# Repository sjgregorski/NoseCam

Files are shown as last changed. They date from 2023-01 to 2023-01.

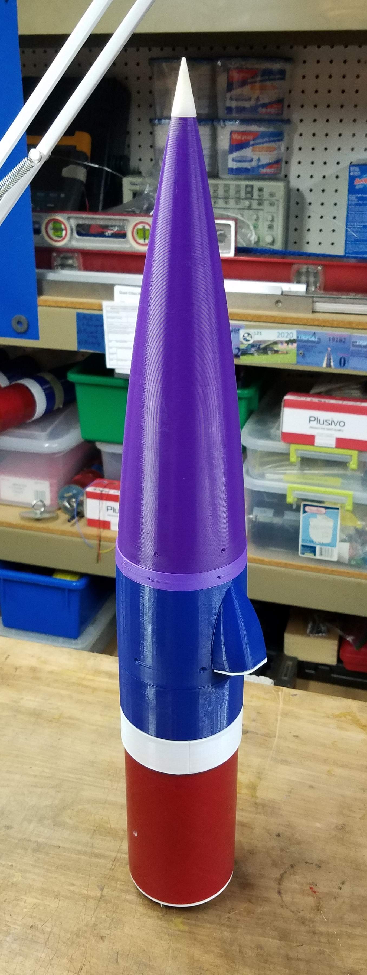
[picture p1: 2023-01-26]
Step 5 - Final Assembly/Build Photos/2023-01-22_019.jpg

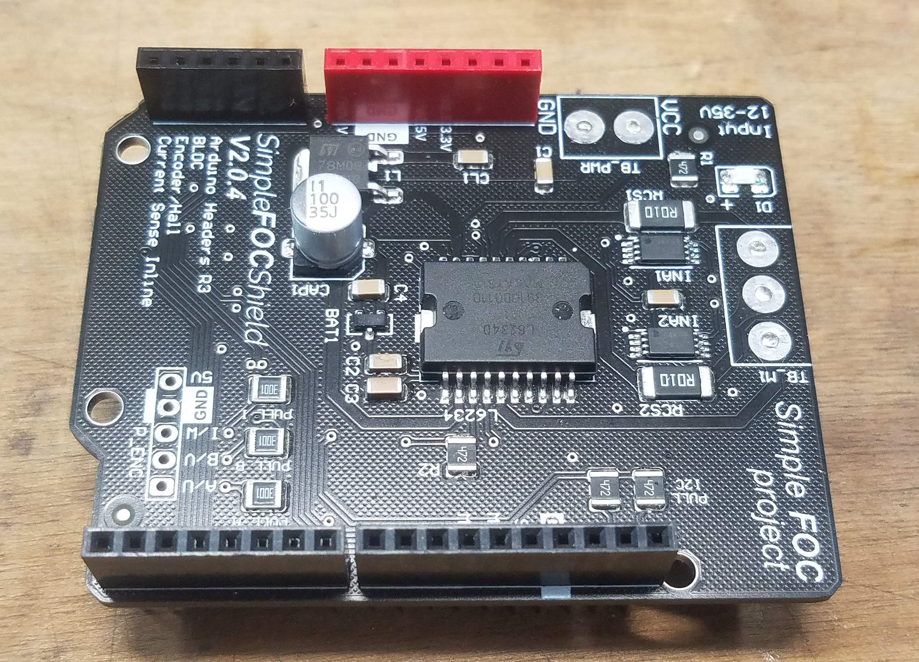
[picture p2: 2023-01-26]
Step 3 - Build the Circuit Board Stack/Build Photos/2023-01-11_013.jpg

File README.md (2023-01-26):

# NoseCam  

NoseCam is something I created to stabilize (de-spin) high power rocket flight videos.  It also forms the basis for a Vertical Orientation Control (VOC) system.  What I am sharing in this distribution does NOT contain info on the VOC subsystem.  That being said, if you manage to successfully build and fly a NoseCam using what I am sharing here then you are 90% of the way to having a VOC system.  Almost everything you need is already here.  You “just” have to add the needed components to the upper nose (servo(s), winglets/canards, etc.) and write some additional code.  

The Rocketry Form (TRF) is where I have been posting everything I’ve been doing with NoseCam.  Here are some useful links to posts:

https://www.rocketryforum.com/threads/a-new-spin-on-vertical-orientation-control.174525/

https://www.rocketryforum.com/threads/falcon-nosecam-build-thread.174591/

https://www.rocketryforum.com/threads/two-stage-flight-with-video-stabilization.172553/

I plan on continuing to use TRF as the only location where I will answer questions.  So if you have a question, post it to the “Falcon NoseCam Build Thread” on TRF.

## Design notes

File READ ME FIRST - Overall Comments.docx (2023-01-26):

NoseCam is something I created to stabilize (de-spin) high power rocket flight videos. It also forms the basis for a Vertical Orientation Control (VOC) system. What I am sharing in this distribution does NOT contain info on the VOC subsystem. That being said, if you manage to successfully build and fly a NoseCam using what I am sharing here then you are 90% of the way to having a VOC system. Almost everything you need is already here. You “just” have to add the needed components to the upper nose (servo(s), winglets/canards, etc.) and write some additional code.

The Rocketry Form (TRF) is where I have been posting everything I’ve been doing with NoseCam. Here are some useful links to posts:

https://www.rocketryforum.com/threads/a-new-spin-on-vertical-orientation-control.174525/

https://www.rocketryforum.com/threads/falcon-nosecam-build-thread.174591/

https://www.rocketryforum.com/threads/two-stage-flight-with-video-stabilization.172553/

I plan on continuing to use TRF as the only location where I will answer questions. So if you have a question, post it to the “Falcon NoseCam Build Thread” on TRF.

What I have provided in this distribution is intended to be a STARTING POINT. It is NOT a complete, soup-to-nuts set of instructions that would allow anyone to build a NoseCam. That would have been far too much work to create. (Sorry) Simply put, if you are going to build one of these things, you are going to need to maintain and tune it. And before you can do those things, you need to understand it. So being an active participant in the overall process (and not just a user) is critical. I’m sure there are things missing in this distribution (such as overall schematics LOL). I’m also very sure there are things wrong that I haven’t found yet. This has been and always will be a research project for me. It is also a work in progress. I consider the Arduino code to be the closest thing there will be to an instruction manual. (Again, sorry) And unfortunately, I write mediocre code at best !

In truth, I don’t have any expectations that someone will build an exact copy of what I have shared here. What I do hope is that like-minded folks can take what I have shared and use some part of it (code, design concepts, etc.) to build something cool for themselves. That being said, if you do try to build a NoseCam using what I have provided here, then you will already need to be VERY GOOD with the following skills:

- High Power Rocketry (HPR) – I have been building and flying for many years and have performed hundreds of high power / electronic dual deploy / GPS tracker flights. I’ve also done a lot of high power two-stage flights. The NoseCam by itself can be a handful to use when you first start out, so it helps if the “rocketry” part of using it is very familiar to you.
- 3D CAD (I use Fusion 360)
  - Modifying / tweaking CAD part files to meet your particular needs
- 3D Printing (and modifying printed parts to fit)
  - These are structural parts going into a rocket. They need strength. PLA printers need not apply.
- Arduino coding and debugging (LOTS and LOTS of debugging)
  - Be prepared to spend a LOT of time mastering the SimpleFOC Arduino library
- Overall mechanical design and fabrication skills
- Electronic design, assembly and debugging (LOTS and LOTS of debugging)

Things you will need:

- Money – I’ve spent several thousand dollars on this. You will spend less, but you will still spend a lot. Plan on buying two or three of everything needed. You will fry / break / trash / crash a lot of stuff. If you buy one set of everything and get it to work and it lasts more than one flight you are a genius.
- Time – I’ve easily spent over 1000 hours developing this. I’ve built several NoseCams, and even with all my experience it takes about 50 hours to build a new one. For someone starting from scratch you should plan on many months of fabrication, learning and mistakes.
- Access to a machine shop / maker space is really helpful. You will definitely need a 3D printer and an electronics assembly bench. Standard debugging tools (DVM, O-Scope, solder rework tools) are a must.

Other stuff:

- There are a lot of “READ ME” files in the various folders. You really want to read all of them. It will save you a LOT of time.
- My expectation is that reading the NoseCam Arduino code will provide enough of an “instruction manual” to get you going. My commenting isn’t great, but it is there. I know it’s a lot of code. But understanding it will be good for you. Just like eating kale ….
- I use Bluetooth classic and my Android phone to communicate with the NoseCam. You can’t use the NoseCam without some way of communicating over Bluetooth. There’s a wonderful Android phone app called “Bluetooth Terminal HC-05 Pro” that I use.

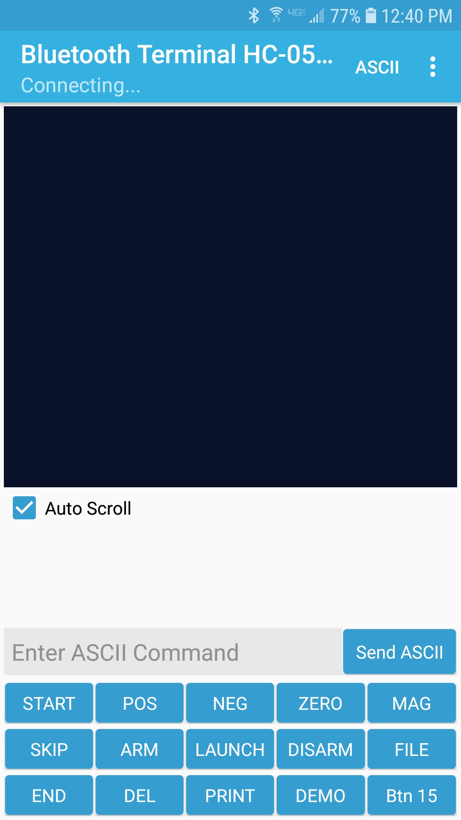
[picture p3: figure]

- The NoseCam Arduino code has data logging for every flight. The data is stored to the 2MB flash on the Adafruit Metro M4. Unfortunately ………….
  - Getting the data off of the NoseCam and into a useful format like Excel is ugly.
    - I connect to the NoseCam with my laptop via Bluetooth
    - I open the Arduino IDE and use the serial monitor to enter the needed commands to get the NoseCam to start streaming the logged data from a particular file to the laptop serial monitor
    - Once the file is done streaming to the serial monitor, I copy-and-paste the data from the serial monitor to a .txt file on my laptop
    - I then open the .txt file as a .csv file in Excel
    - I told you it was ugly
  - I download data after every flight and then delete the data file from the NoseCam since there is only 2MB of flash storage there. I have no idea how many data files can be written to the flash before some weird file management error occurs. You have been warned 😊
- I’ll put this info here and repeat it in other places
  - Use the 1.7.5 version of the Adafruit SAMD board library for the Metro M4. Do NOT use the latest version. It will not work. I have no idea why.
  - Use the SimpleFOC libraries I have provided it this distribution. They are an older version but they work. Do NOT try to download and use the latest version of the libraries. They will not work. I have no idea why.
    - Just FYI, my SimpleFOC libraries have two slight modifications which make synchronizing the BLDC motor to the encoder less aggressive.

That’s it ! Good luck !!!!!!!

Steve Gregorski

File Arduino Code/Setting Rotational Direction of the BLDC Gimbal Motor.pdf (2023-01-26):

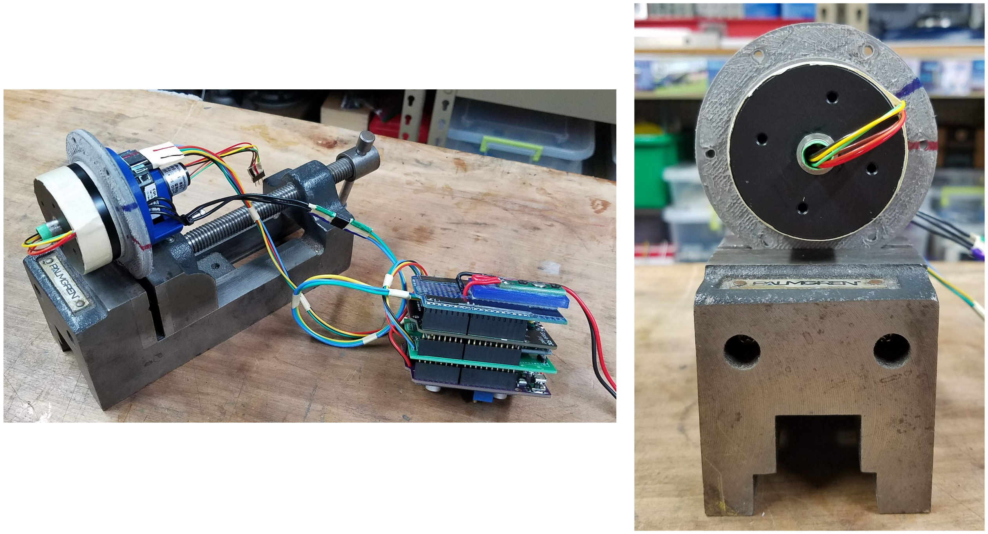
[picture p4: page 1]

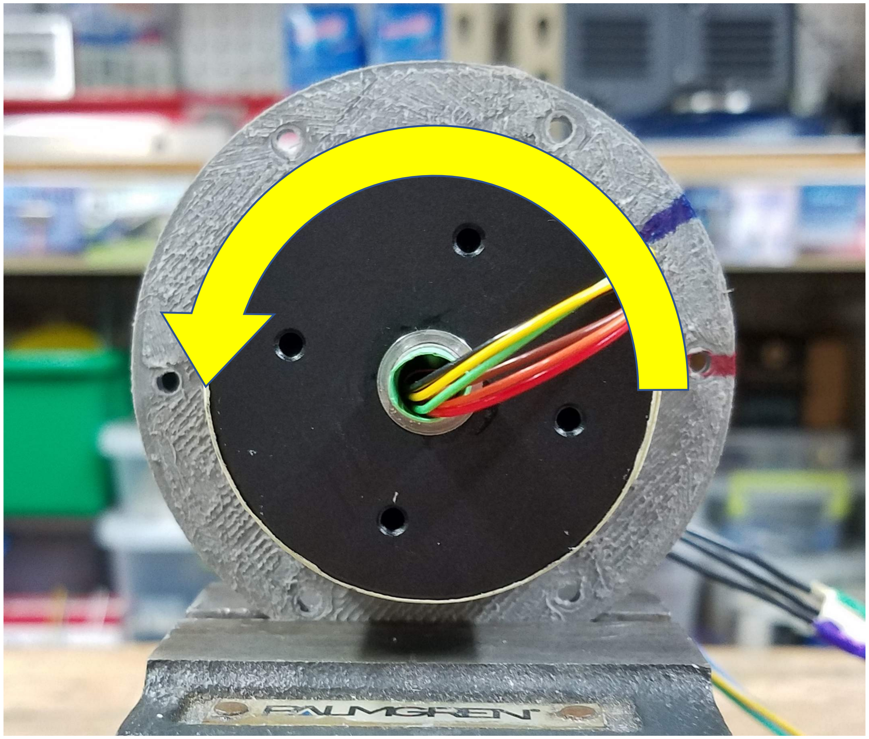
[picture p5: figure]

Correct direction of rotation when commanding a POSITIVE rotational velocity

If the motor rotates the wrong way, then swap any two connections on the leads between the brushless motor and the drive amplifier

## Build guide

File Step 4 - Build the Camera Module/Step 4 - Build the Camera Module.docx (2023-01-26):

No surprise – the RunCam Split 3 Lite is delicate. Don’t tug on the wiring.

Two important things about the RunCam Split 3 Lite:

1) It starts recording as soon as power is applied

2) It can take a wide range of input power voltage

The main chip on the camera processor board gets really hot. Make sure to use thermal grease between the chip surface and the aluminum rod heatsink

In the photos there is a plastic screw coming out of the end of the aluminum heatsink rod. Ignore it. It has no purpose.

The camera module is attached to the power head with #2 flathead stainless screws. These are not shown in the photos.

The fit between the camera module and the power head is nice and tight. I use a lathe on the power head interface piece to adjust its OD to match the ID of the camera module.

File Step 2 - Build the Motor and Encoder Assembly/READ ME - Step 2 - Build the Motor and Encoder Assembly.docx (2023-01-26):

A short length of thin wall stainless steel tube is glued into the motor thru hole. The tube is 5/16” OD (~8mm). It’s main purpose is to provide a mount for the rotary encoder. It also provides a pass-thru for wires from the electrical slip ring.

I line the inside of the stainless tube with heat shrink tubing to prevent the pass-thru wires from rubbing against the steel.

It’s important that the tube OD is as concentric as possible with the motor thru-hole. I build up the OD with adhesive and then turn it down on a lathe to get a tight fit.

I do NOT use the index pulse on the CUI Devices AMT10E3-V encoder to determine a “ZERO” position. I have found (for whatever reason) that the index pulse on this particular encoder can be buggy.

The encoder is configured to a resolution [PPR] of 2560 via the onboard switches

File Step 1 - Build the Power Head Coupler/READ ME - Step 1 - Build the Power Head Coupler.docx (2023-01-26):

Coupler tube is Wildman 3” FWFG

Use CAD files to 3D Print needed parts

Adjust all CAD files as needed and trim / sand / machine parts to obtain a good fit

Glue six 4-40 nuts to the underside of the flange

Screws are temporarily used to hold the nuts in place while the epoxy cures

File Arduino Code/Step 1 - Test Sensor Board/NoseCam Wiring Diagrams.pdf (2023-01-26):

- Bluetooth

→ Bluetooth

3.3V To 6DOF
Modules on SPI
Also To Encoder

5V to Bluetooth

8V from Buck Regulator

Current Sense from
SimpleFOC
Driver Board
- Encoder Phase A
- Encoder Phase B
- Encoder Index

→ PWM A

→ PWM B

SimpleFOC PWM
outputs only work on
some pins, even
though most M4 pins
are “PWM capable”

→ PWM C

→ Amplifier Enable

→ SPI CS for Sensor 1

→ SPI CS for Sensor 2

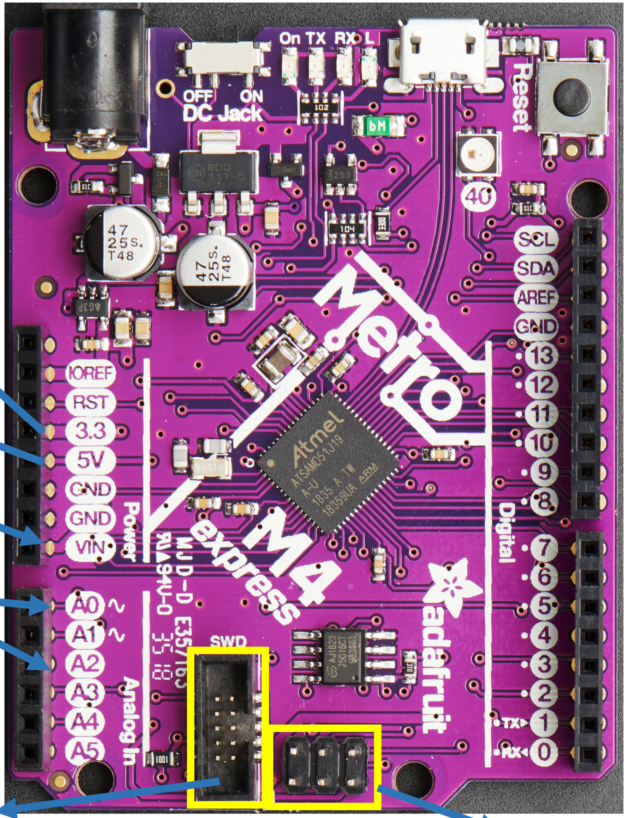
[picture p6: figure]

Common SPI Pins to Sensors

Available 3.3V and
GND (not used)

→ On/Off Camera and Servo

Servo Chan. 1

Servo Chan. 2

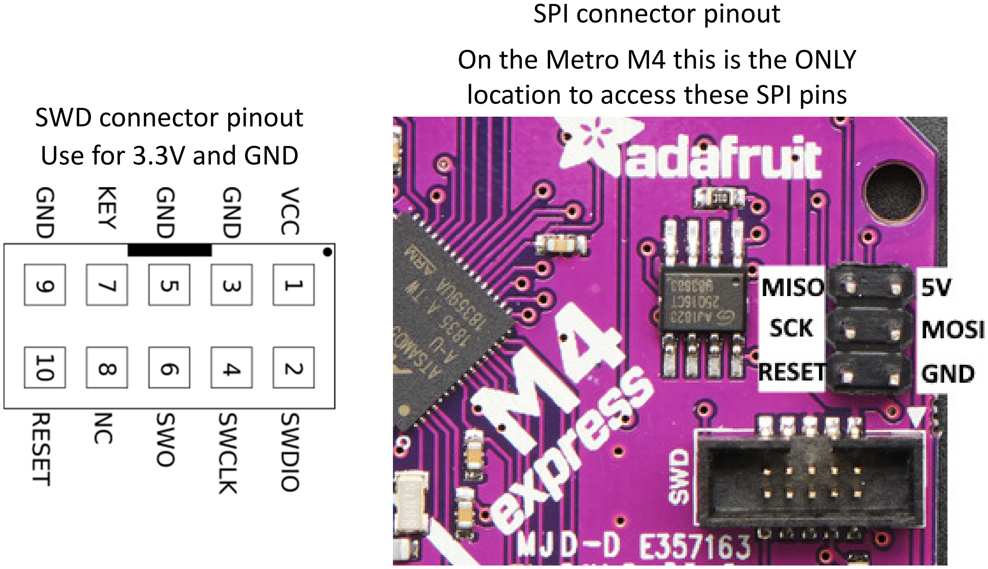
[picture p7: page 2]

SPI connector pinout

On the Metro M4 this is the ONLY location to access these SPI pins SWD connector pinout

Use for 3.3V and GND

## Adafruit ISM330DHCX SPI Connections

All pins going into the breakout have level shifting circuitry to make them 3-5V logic level safe. Use whatever logic level is on Vin

SCK - This is also the SPI Clock pin, it's an input to the chip
DO (Bottom) - this is the serial Data Out / Microcontroller In Sensor Out pin, for data sent from the LSM6DSOX, ISM330DHCX, or LSM6DSO32 to your processor.
SDA - this is also the Serial Data In / Microcontroller Out Sensor In pin, for data sent from your processor to the LSM6DSOX, ISM330DHCX, or LSM6DSO32
CS (Bottom) - this is the Chip Select pin, drop it low to start an SPI transaction. Its an input to the chip

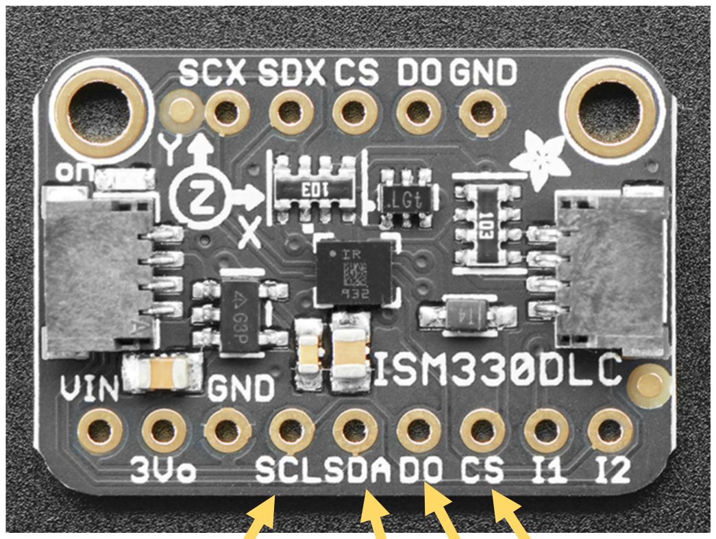
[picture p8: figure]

MISO

CS

MOSI

SCK

## Adafruit ICM20649

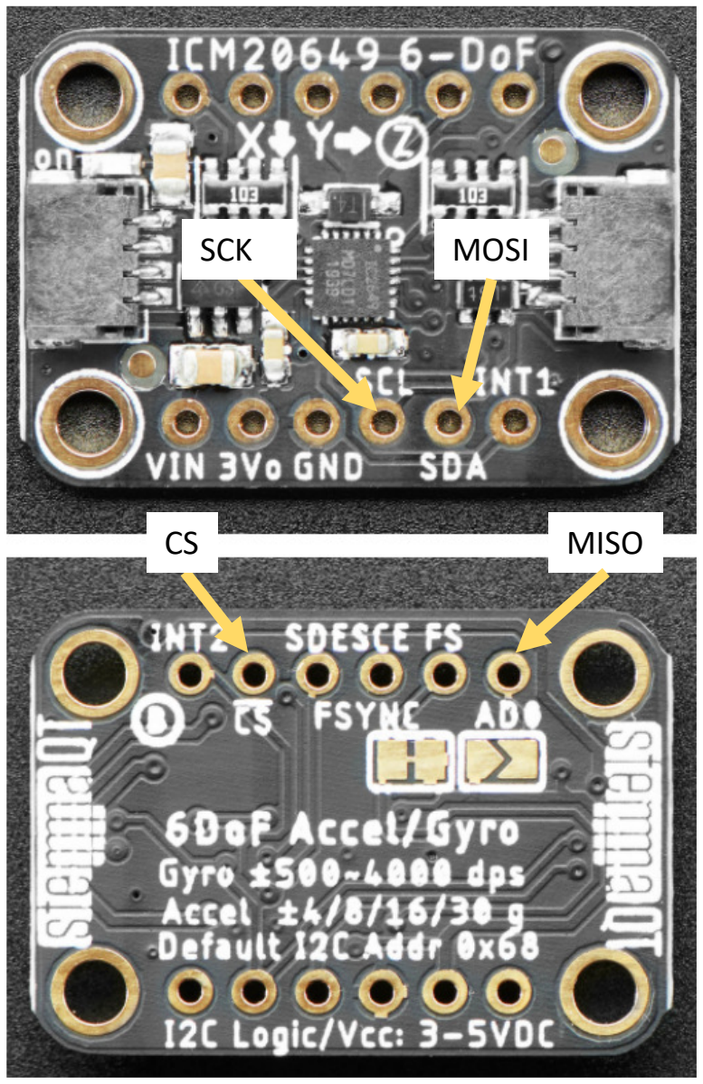
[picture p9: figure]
MISO; SCK; MOSI

## SPI Connections

All pins going into the breakout have level shifting circuitry to make them 3-5V logic level safe. Use whatever logic level is on Vin

SCL (SCK)- This is also the SPI Clock pin, it's an input to the chip
SDA (MOSI) - this is also the Serial Data In / Microcontroller Out Sensor In pin, for data sent from your processor to the sensor AD0 (MISO) - this is the Serial Data Out / Microcontroller In Sensor Out pin, for data sent from the sensor to your processor.
CS - this is the Chip Select pin, drop it low to start an SPI transaction. Its an input to the chip

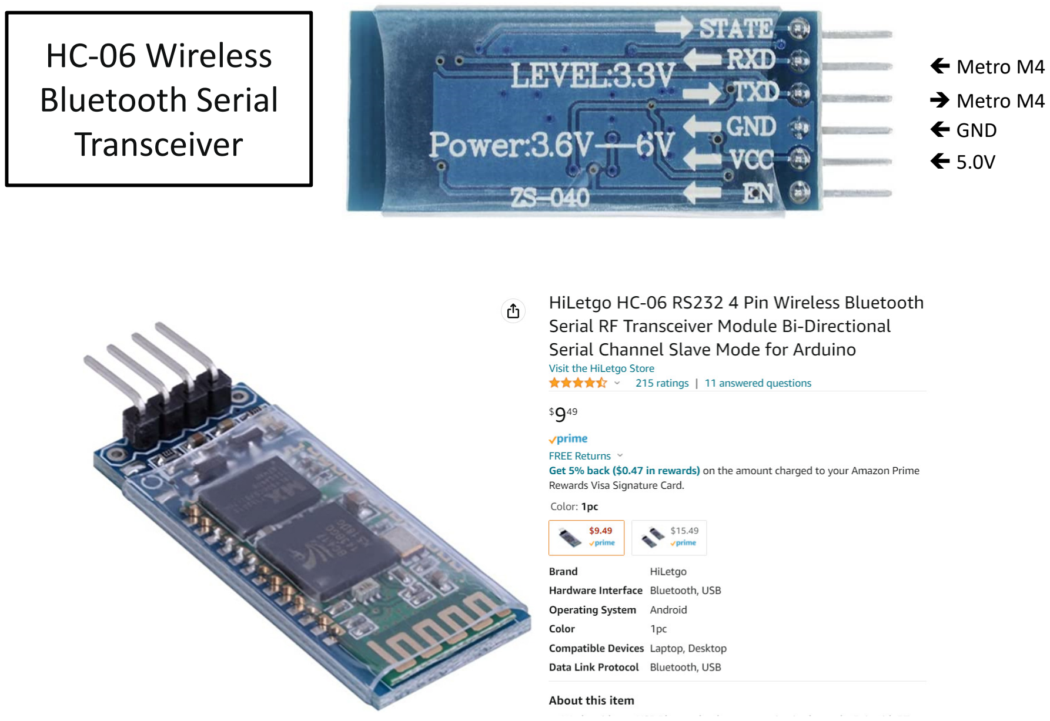
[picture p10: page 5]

→ Metro M4
- GND

### HC-06 Wireless Bluetooth Serial Transceiver

- 5.0V
- Metro M4

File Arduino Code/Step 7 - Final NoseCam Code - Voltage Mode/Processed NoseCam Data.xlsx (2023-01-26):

Time[s] | Spin Rate DPS | Lat Accel Mag | Accel Z | Accel2 Z | Vel m/s | Alt m | Z Gyro Degs | Z Gyro2 Degs | Tilt Degs | Tilt2 Degs | EWMA Euler Tilt Bearing | EWMA Euler Tilt Bearing2 | Motor Pos Setpoint Degs | Motor Pos Error Degs | Accel Altitude [ft] | Max accel Altitude [ft]
0.005 | -0.05 | 0.135 | 0.991 | 0.975 | 0.20 | 0.0 | 0 | 0 | 7.7 | 7.0 | 0.0 | 0.0 | 0.000 | 6.258 | 0 | 0.656168 | Pre-Launch Roll Pitch and Tilt Degs From Accel: |  |  |  | -0.92 | 7.68 | 7.74
0.035 | -4.65 | 0.130 | 0.996 | 0.968 | 0.20 | 0.0 | 0 | 0 | 7.7 | 7.0 | 0.0 | 0.0 | 0.297 | 4.750 | 0 |  | Gyro Zero Rate Offset: |  |  |  | -0.00143 | -0.00900 | 0.00117
0.065 | 3 | 0.139 | 0.997 | 0.985 | 0.20 | 0.0 | 0 | 0 | 7.7 | 7.0 | 0.0 | 0.0 | 0.253 | 3.252 | 0 |  | Gyro2 Zero Rate Offset: |  |  |  | 0.00685 | 0.00678 | -0.00619
0.095 | -2 | 0.135 | 0.989 | 0.973 | 0.20 | 0.0 | 0 | 0 | 7.7 | 7.0 | 0.0 | 0.0 | -0.443 | 2.081 | 0
0.125 | 1.3 | 0.131 | 0.992 | 0.977 | 0.20 | 0.0 | 0 | 0 | 7.7 | 7.0 | 0.0 | 0.0 | -0.023 | 1.363 | 0
0.155 | 1.6 | 0.141 | 0.993 | 0.973 | 0.20 | 0.0 | 0 | 0 | 7.7 | 7.0 | 0.0 | 0.0 | 0.179 | 0.606 | 0
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

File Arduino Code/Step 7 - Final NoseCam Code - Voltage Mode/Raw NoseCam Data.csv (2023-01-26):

Time[s] | Spin Rate DPS | Lat Accel Mag | Accel Z | Accel2 Z | Vel m/s | Alt m | Z Gyro Degs | Z Gyro2 Degs | Tilt Degs | Tilt2 Degs | EWMA Euler Tilt Bearing | EWMA Euler Tilt Bearing2 | Motor Pos Setpoint Degs | Motor Pos Error Degs
Pre-Launch Roll Pitch and Tilt Degs From Accel: |  |  |  |  | -0.92 | 7.68 | 7.74
Gyro Zero Rate Offset: |  |  |  |  | -0.001430 | -0.008997 | 0.001167
Gyro2 Zero Rate Offset: |  |  |  |  | 0.006854 | 0.006781 | -0.006190
0.005202 | -0.05 | 0.135 | 0.991 | 0.975 | 0.20 | 0.0 | 0 | 0 | 7.7 | 7.0 | 0.00 | 0.00 | 0.000 | 6.258
0.035206 | -4.65 | 0.130 | 0.996 | 0.968 | 0.20 | 0.0 | 0 | 0 | 7.7 | 7.0 | 0.00 | 0.00 | 0.297 | 4.750
0.065212 | 3.00 | 0.139 | 0.997 | 0.985 | 0.20 | 0.0 | 0 | 0 | 7.7 | 7.0 | 0.00 | 0.00 | 0.253 | 3.252
0.095216 | -2.00 | 0.135 | 0.989 | 0.973 | 0.20 | 0.0 | 0 | 0 | 7.7 | 7.0 | 0.00 | 0.00 | -0.443 | 2.081
0.125221 | 1.30 | 0.131 | 0.992 | 0.977 | 0.20 | 0.0 | 0 | 0 | 7.7 | 7.0 | 0.00 | 0.00 | -0.023 | 1.363
0.155227 | 1.60 | 0.141 | 0.993 | 0.973 | 0.20 | 0.0 | 0 | 0 | 7.7 | 7.0 | 0.00 | 0.00 | 0.179 | 0.606
0.185232 | -1.20 | 0.129 | 0.993 | 0.974 | 0.20 | 0.0 | 0 | 0 | 7.7 | 7.0 | 0.00 | 0.00 | 0.016 | 0.032
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

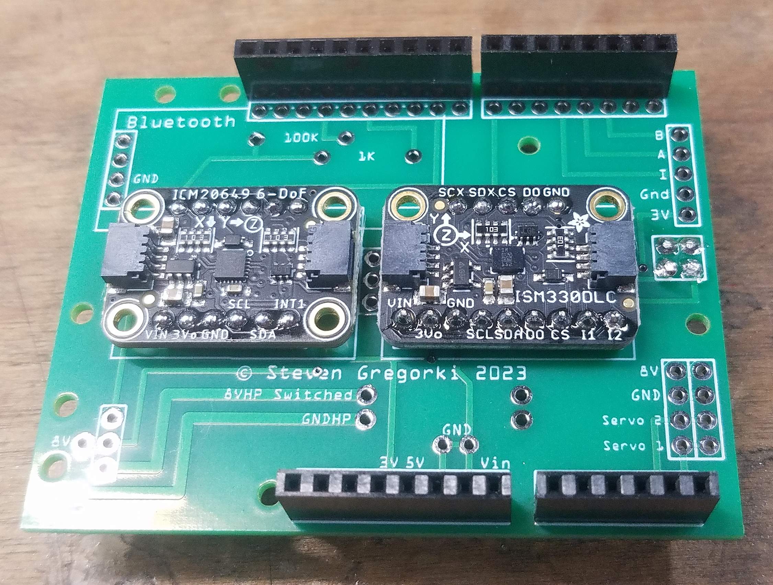
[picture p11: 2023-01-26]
Step 3 - Build the Circuit Board Stack/Build Photos/2023-01-11_022.jpg

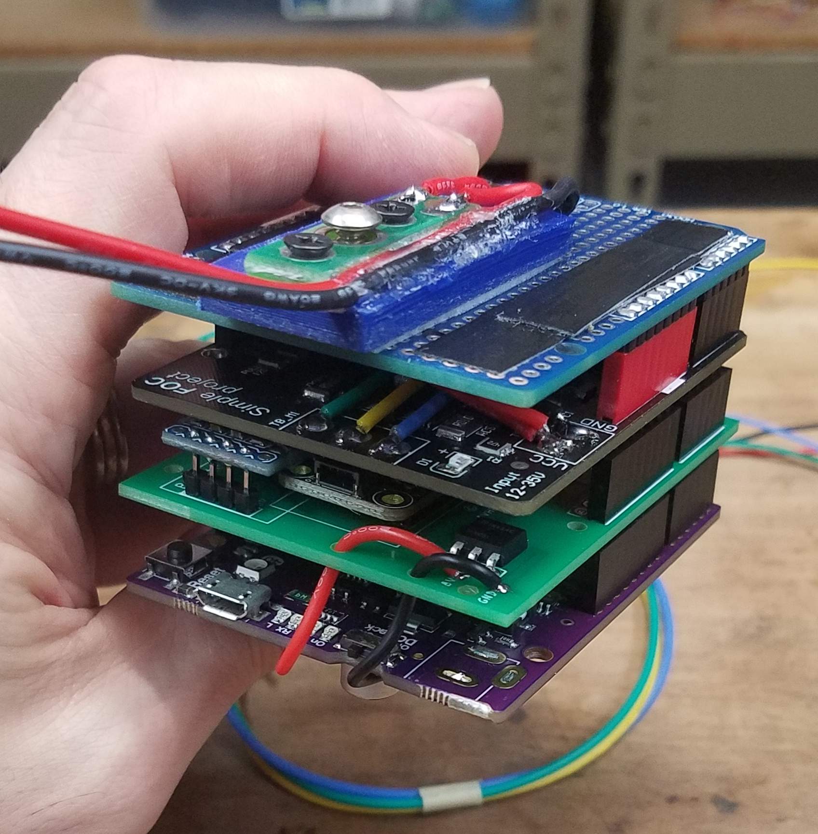
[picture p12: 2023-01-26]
Step 3 - Build the Circuit Board Stack/Build Photos/2023-01-14_015.jpg

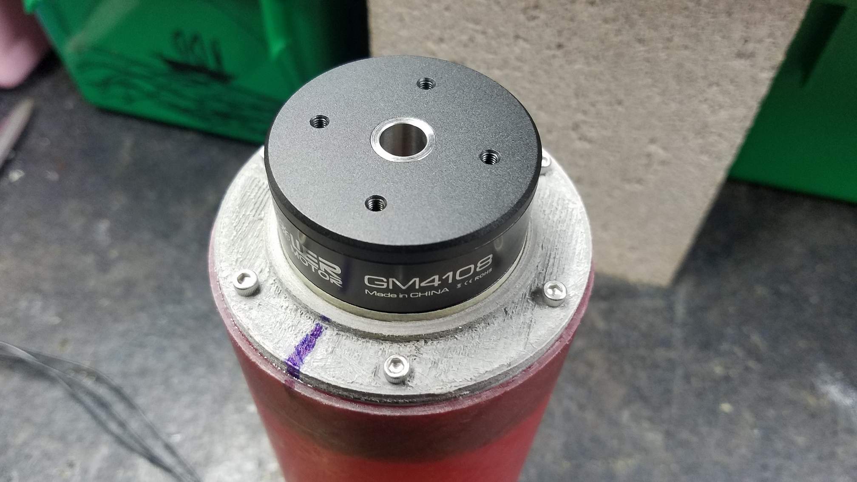
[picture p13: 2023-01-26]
Step 2 - Build the Motor and Encoder Assembly/Build Photos/2022-12-03_040.jpg

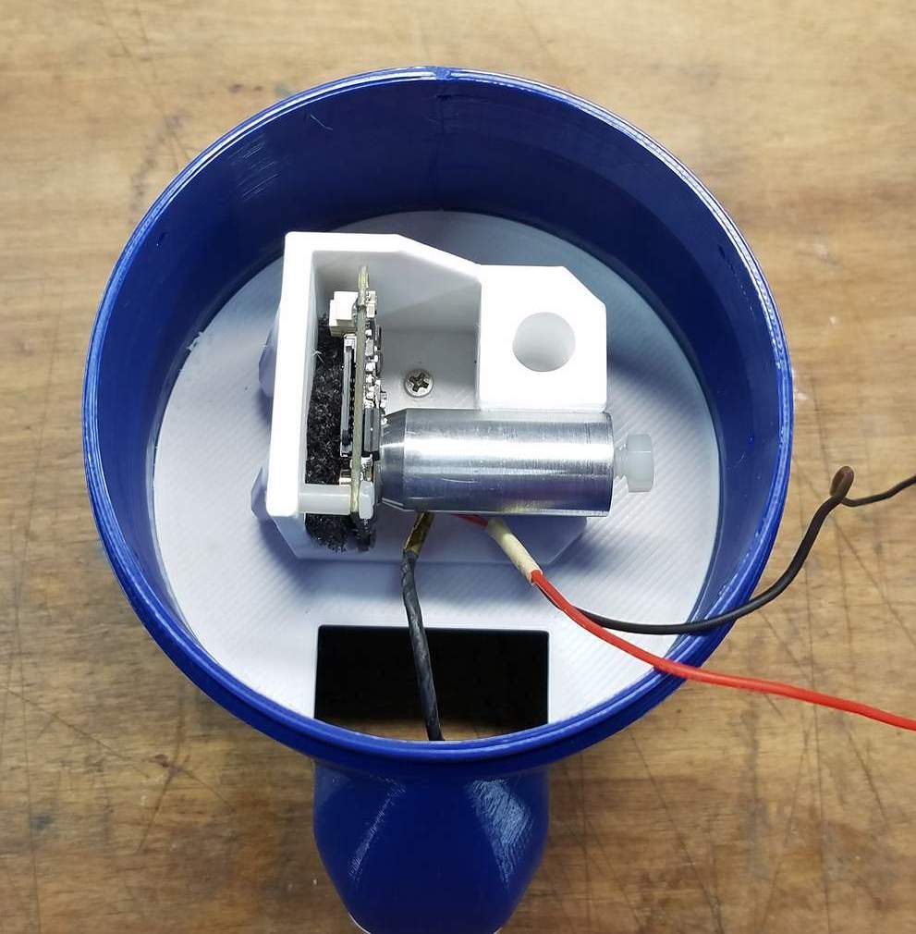
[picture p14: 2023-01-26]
Step 4 - Build the Camera Module/Build Photos/2022-12-03_047.jpg

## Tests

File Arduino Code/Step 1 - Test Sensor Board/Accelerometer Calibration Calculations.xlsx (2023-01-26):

ISM330DHCX
Native X Axis | Raw Data | Offset From Avg |  | Scaling Factor | Final Values
Max: | 9.80 | 0.005 | 9.795 | 1.001531 | 9.81
Min: | -9.79 |  | -9.795 |  | -9.81
Native Y Axis
Max: | 9.56 | -0.270 | 9.83 | 0.997965 | 9.81
Min: | -10.10 |  | -9.83 |  | -9.81
Native Z Axis
Max: | 9.96 | 0.138 | 9.818 | 0.999185 | 9.81
Min: | -9.68 |  | -9.818 |  | -9.81
ICM20649
Native X Axis | Raw Data | Offset From Avg |  | Scaling Factor | Final Values
Max: | 9.83 | -0.005 | 9.835 | 0.997458 | 9.81
Min: | -9.84 |  | -9.835 |  | -9.81
Native Y Axis
Max: | 9.63 | -0.195 | 9.825 | 0.998473 | 9.81
Min: | -10.02 |  | -9.825 |  | -9.81
Native Z Axis
Max: | 10.02 | 0.060 | 9.96 | 0.984940 | 9.81
Min: | -9.90 |  | -9.96 |  | -9.81

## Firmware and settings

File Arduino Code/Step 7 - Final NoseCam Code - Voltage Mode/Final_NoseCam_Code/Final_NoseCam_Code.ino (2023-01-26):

#include <SimpleFOC.h>
#include <SPI.h>
#include <SdFat.h>
#include <Adafruit_SPIFlash.h>

#include <Adafruit_ISM330DHCX.h>
#include <Adafruit_ICM20X.h>
#include <Adafruit_ICM20649.h>

// For SPI mode, we need a CS pin
#define LSM_CS 7
#define ICM_CS 9

#define POWER_SWITCH 12   // Pin 12 controls power to the camera
#define LED 13

#define PulsesPerRev 2560


// On-board external flash (QSPI or SPI) macros should already
// defined in your board variant if supported
// - EXTERNAL_FLASH_USE_QSPI
// - EXTERNAL_FLASH_USE_CS/EXTERNAL_FLASH_USE_SPI
#if defined(EXTERNAL_FLASH_USE_QSPI)
  Adafruit_FlashTransport_QSPI flashTransport;
#elif defined(EXTERNAL_FLASH_USE_SPI)
  Adafruit_FlashTransport_SPI flashTransport(EXTERNAL_FLASH_USE_CS, EXTERNAL_FLASH_USE_SPI);
#else
  #error No QSPI/SPI flash are defined on your board variant.h !
#endif

Adafruit_SPIFlash flash(&flashTransport);


// file system object from SdFat
FatFileSystem fatfs;
File DataFile;


// objects for the two 6DOF sensor modules
Adafruit_ISM330DHCX ism330dhcx;
Adafruit_ICM20649 icm20649;
sensors_event_t accel, gyro, temp;


// BLDC motor & driver instance
BLDCMotor motor = BLDCMotor(11); // 11 pole pairs
// Only certain pins can be used on the Metro M4 - e.g. pin 9 will NOT work
BLDCDriver3PWM driver = BLDCDriver3PWM(10, 5, 6, 8);

Encoder encoder = Encoder(2, 3, PulsesPerRev);

// interrupt routine intialization
void doA(){encoder.handleA();}
void doB(){encoder.handleB();}

// commander communication instance
Commander command = Commander(Serial1);
float P_Base, P_Gain, D_Base, D_Gain, Spin_Rate_Adj;
float Z_Gyro_Cal, Z_Gyro2_Cal;
void onMotor(char* cmd){ command.motor(&motor, cmd); }
void P_Base_Call(char* cmd){ command.scalar(&P_Base, cmd); }
void P_Gain_Call(char* cmd){ command.scalar(&P_Gain, cmd); }
void D_Base_Call(char* cmd){ command.scalar(&D_Base, cmd); }
void D_Gain_Call(char* cmd){ command.scalar(&D_Gain, cmd); }
void Rate_Adj_Call(char* cmd){ command.scalar(&Spin_Rate_Adj, cmd); }
void Z_Gyro_Call(char* cmd){ command.scalar(&Z_Gyro_Cal, cmd); }
void Z_Gyro2_Call(char* cmd){ command.scalar(&Z_Gyro2_Cal, cmd); }

char* my_string; 

uint32_t prev_micros_timer = micros();
uint32_t micros_timer = micros();
uint32_t loop_duration_micros;
uint32_t target_loop_rate_us = 10000;
uint32_t BLDC_loop_duration_us = 333;
uint32_t loop_timer = micros();
uint32_t Runtime = millis();
uint32_t Starttime = micros();
uint32_t Timer1 = micros();
uint32_t Timer2 = micros();
uint32_t PrevConversionTimer = micros();
uint32_t ConversionTimer = micros();
uint32_t ConversionTimeMicros;
uint32_t PrevConversionTimer2 = micros();
uint32_t ConversionTimer2 = micros();
uint32_t ConversionTime2Micros;

int loopcount = 0;
int memorycount = 0;
int retract_count = 0;
int number_of_files = 0;


// Since there are two independent 6DOF sensor modules
// there are "two of everything" with respect to
// accelerometer and gyro varibles

float accel_x_vert, accel_y_vert, accel_z_vert;
float gyro_x_vert, gyro_y_vert, gyro_z_vert;
float accel2_x_vert, accel2_y_vert, accel2_z_vert;
float gyro2_x_vert, gyro2_y_vert, gyro2_z_vert;

float raw_accel_x_offset, raw_accel_y_offset, raw_accel_z_offset;
float raw_accel_x_scaling, raw_accel_y_scaling, raw_accel_z_scaling;
float raw_accel_x_corrected, raw_accel_y_corrected, raw_accel_z_corrected;

float raw_accel2_x_offset, raw_accel2_y_offset, raw_accel2_z_offset;
float raw_accel2_x_scaling, raw_accel2_y_scaling, raw_accel2_z_scaling;
float raw_accel2_x_corrected, raw_accel2_y_corrected, raw_accel2_z_corrected;

float accel_x_norm, accel_y_norm, accel_z_norm, accel_magnitude;
float pitch_rads_from_accel, yaw_rads_from_accel, pitch_degs_from_accel, yaw_degs_from_accel;
float accel_x_old_ewma, accel_y_old_ewma, accel_z_old_ewma;
float accel_x_ewma, accel_y_ewma, accel_z_ewma;
float gyro_x_old_ewma, gyro_y_old_ewma, gyro_z_old_ewma;
float gyro_x_ewma, gyro_y_ewma, gyro_z_ewma;

float accel2_x_norm, accel2_y_norm, accel2_z_norm, accel2_magnitude;
float pitch_rads_from_accel2, yaw_rads_from_accel2, pitch_degs_from_accel2, yaw_degs_from_accel2;
float accel2_x_old_ewma, accel2_y_old_ewma, accel2_z_old_ewma;
float accel2_x_ewma, accel2_y_ewma, accel2_z_ewma;
float gyro2_x_old_ewma, gyro2_y_old_ewma, gyro2_z_old_ewma;
float gyro2_x_ewma, gyro2_y_ewma, gyro2_z_ewma;

float gyro_x_offset, gyro_y_offset, gyro_z_offset;
float gyro2_x_offset, gyro2_y_offset, gyro2_z_offset;

float PID_Setpoint_rads;
float PID_Setpoint_degs;
float rotary_encoder_rads;
float position_error_rads;
float position_error_degs;
float CurrentPositionRads = 0, PreviousPositionRads = 0;
float encoder_offset_rads;

float spin_rate_dps;
float prev_vel_mps = 0, vel_mps = 0, vert_vel_mps = 0;
float prev_alt_m = 0, alt_m = 0;

float spin_rate2_dps;
float prev_vel2_mps = 0, vel2_mps = 0, vert_vel2_mps = 0;
float prev_alt2_m = 0, alt2_m = 0;

float x_angle_rads_increment;
float y_angle_rads_increment;
float z_angle_rads_increment;

float x_angle2_rads_increment;
float y_angle2_rads_increment;
float z_angle2_rads_increment;

// float x_angle_rads_from_simple_intg;  // not needed
// float y_angle_rads_from_simple_intg;  // not needed
float z_angle_rads_from_simple_intg;

// float x_angle2_rads_from_simple_intg;  // not needed
// float y_angle2_rads_from_simple_intg;  // not needed
float z_angle2_rads_from_simple_intg;

// float x_angle_degs_from_simple_intg; // not needed
// float y_angle_degs_from_simple_intg; // not needed
float z_angle_degs_from_simple_intg;

// float x_angle2_degs_from_simple_intg; // not needed
// float y_angle2_degs_from_simple_intg; // not needed
float z_angle2_degs_from_simple_intg;

float Pad_Ref_Yaw_Component_Rads;
float Pad_Ref_Pitch_Component_Rads;

float Pad_Ref_Yaw2_Component_Rads;
float Pad_Ref_Pitch2_Component_Rads;

float Pad_Ref_Yaw_Component_Degs;
float Pad_Ref_Pitch_Component_Degs;

float Pad_Ref_Yaw2_Component_Degs;
float Pad_Ref_Pitch2_Component_Degs;

float bearing_deg_from_intg_z_rotation;
float delta_bearing_deg_from_intg_z_rotation;
float windup_bearing_deg_from_intg_z_rotation;

float bearing2_deg_from_intg_z_rotation;
float delta_bearing2_deg_from_intg_z_rotation;
float windup_bearing2_deg_from_intg_z_rotation;

float tilt_bearing_deg;
float prev_tilt_bearing_deg;
float tilt_bearing_difference;
float delta_tilt_bearing_deg;
float windup_tilt_bearing_deg;
float EWMA_windup_tilt_bearing_deg;

float tilt_bearing2_deg;
float prev_tilt_bearing2_deg;
float tilt_bearing2_difference;
float delta_tilt_bearing2_deg;
float windup_tilt_bearing2_deg;
float EWMA_windup_tilt_bearing2_deg;

float delta_error_signal;
float windup_error_signal;

float delta_error_signal2;
float windup_error_signal2;

float a, b, c, e, tilt, tilt_rads;
float tilt_on_pad;

float a2, b2, c2, e2, tilt2, tilt2_rads;
float tilt2_on_pad;

boolean START = false;
boolean STOP = false;
boolean DEMO = false;
boolean START_FILE = false;
boolean STOP_TEST = false;
boolean ZERO = false;
boolean SKIP = false;
boolean ARM = false;
boolean LAUNCH = false;
boolean APOGEE = false;
boolean COMPLETE = false;
boolean TILT_LIMIT = false;
boolean MOTOR_DISABLE = false;
boolean ISM330DHCX_CONVERSION = false;
boolean START_DATA_LOGGING = false;
boolean toggle;
String Incoming;


uint32_t time_array[2001];
int16_t spin_rate_dps_array[2001];
int16_t lat_accel_mag[2001];
int16_t accel_z_vert_array[2001];
int16_t accel2_z_vert_array[2001];
int16_t vel_mps_array[2001];
uint16_t alt_m_array[2001];
int16_t bearing_deg_from_intg_z_rotation_array[2001];
int16_t bearing2_deg_from_intg_z_rotation_array[2001];
int16_t tilt_degs_array[2001];
int16_t tilt2_degs_array[2001];
int16_t tilt_bearing_deg_array[2001];
int16_t tilt_bearing2_deg_array[2001];
float motor_pos_setpoint_array[2001];
float motor_pos_error_array[2001];


/*-------------------------------------------------------------------------------------------------*/
/*-------------------------------------------------------------------------------------------------*/  


#include "9_Subroutines.h"


/*-------------------------------------------------------------------------------------------------*/
/*-------------------------------------------------------------------------------------------------*/  


void setup() {

  Serial.begin(115200);  // USB connection
  Serial1.begin(57600);  // Bluetooth connection

  pinMode(POWER_SWITCH, OUTPUT);  // Pin 12 controls power to the camera
  digitalWrite(POWER_SWITCH, LOW);
  
  delay(2000);

  Serial.println("\n\nInitializing Onboard Flash File System\n");
  Serial1.println("\n\nInitializing Onboard Flash File System\n");
  
  // Init external flash
  flash.begin();

  // Init file system on the flash
  fatfs.begin(&flash);

  Serial.println("Filesystem Initialized\n\n");
  Serial1.println("Filesystem Initialized\n\n");
  
  delay(500);


  /*-------------------------------------------------------------------------------------------------*/
  /*-------------------------------------------------------------------------------------------------*/  


  #include "1_Setup_Param.h"


  /*-------------------------------------------------------------------------------------------------*/
  /*-------------------------------------------------------------------------------------------------*/  


  while (!START) {

  Serial1.println("Type START to begin");
  Serial1.println("Type DEMO for accel-only demo");  
  Serial1.println("Type FILE for file operations\n");    
  delay(1000);
  
    while (!START && !DEMO && !START_FILE && Serial1.available() > 0) {   
      // get the new byte:
      char inChar = Serial1.read();
      // add it to the inputString:
      Incoming += inChar;    
      if (inChar == '\n') {
        Serial1.println(Incoming);
        
        if (Incoming.indexOf("START") >= 0) {
          Serial1.println("System Started\n\n\n");
          START = true;
        }

        else if (Incoming.indexOf("DEMO") >= 0) {
          Serial1.println("System Started\n\n\n");
          START = true;
          DEMO = true;          
        }

        else if (Incoming.indexOf("FILE") >= 0) {
          START_FILE = true;
          File_Operations();
        }

        else Serial1.println("No Match\n");
          
        Incoming = "";   
          
      }
           
    }

  }

  while (Serial1.available() > 0) Serial1.read(); // clear buffer

  delay(500);


  /*-------------------------------------------------------------------------------------------------*/
  /*-------------------------------------------------------------------------------------------------*/  


  #include "4_SensorActivate.h"


  /*-------------------------------------------------------------------------------------------------*/
  /*-------------------------------------------------------------------------------------------------*/  


  #include "3_EncoderZero.h"


  /*-------------------------------------------------------------------------------------------------*/
  /*-------------------------------------------------------------------------------------------------*/  


  // Optional code for testing purposes
  // Edit "2_TestingCode.h" as necessary
  // #include "2_TestingCode.h"


  /*-------------------------------------------------------------------------------------------------*/
  /*-------------------------------------------------------------------------------------------------*/  


  #include "6_DemoCode.h"


  /*-------------------------------------------------------------------------------------------------*/
  /*-------------------------------------------------------------------------------------------------*/  


  #include "5_Arm_And_Wait.h"


  /*-------------------------------------------------------------------------------------------------*/
  /*-------------------------------------------------------------------------------------------------*/  


  // The code below is run at the moment the launch is detected

  motor.velocity_limit = 40;
  motor.P_angle.limit = 40; // MUST follow changes to motor.velocity_limit

  motor.PID_velocity.P = 0.50000;
  motor.PID_velocity.I = 5.00000;
  motor.PID_velocity.D = 0.00000;
  motor.LPF_velocity.Tf = 0.005;   // velocity low pass filtering time constant   // smaller means less filtering
  motor.P_angle.P = 20;   // angle loop PID controller parameters   // not used for torque or velocity control
  motor.P_angle.I = 0;
  motor.P_angle.D = 0;  

  // x_angle_rads_from_simple_intg = 0;  // not needed
  // y_angle_rads_from_simple_intg = 0;   // not needed
  z_angle_rads_from_simple_intg = 0;

  // x_angle2_rads_from_simple_intg = 0;  // not needed
  // y_angle2_rads_from_simple_intg = 0;  // not needed
  z_angle2_rads_from_simple_intg = 0;
  
  bearing_deg_from_intg_z_rotation = 0;
  delta_bearing_deg_from_intg_z_rotation = 0;  
  windup_bearing_deg_from_intg_z_rotation = 0;

  bearing2_deg_from_intg_z_rotation = 0;
  delta_bearing2_deg_from_intg_z_rotation = 0;  
  windup_bearing2_deg_from_intg_z_rotation = 0;

  // Record gyro offsets
  gyro_x_offset = gyro_x_ewma;
  gyro_y_offset = gyro_y_ewma;
  gyro_z_offset = gyro_z_ewma;

  gyro2_x_offset = gyro2_x_ewma;
  gyro2_y_offset = gyro2_y_ewma;
  gyro2_z_offset = gyro2_z_ewma;

  // Initialize the gyro-based yaw and pitch using the
  // accelerometer-based yaw and pitch from the pre-launch pad conditions
  // Yaw is the same as the "left to right" tilt on the pad
  // Pitch is same as the "forward to back" tilt on the pad 
  Pad_Ref_Yaw_Component_Rads = yaw_rads_from_accel;
  Pad_Ref_Pitch_Component_Rads = pitch_rads_from_accel;

  Pad_Ref_Yaw2_Component_Rads = yaw_rads_from_accel2;
  Pad_Ref_Pitch2_Component_Rads = pitch_rads_from_accel2;
  
  prev_tilt_bearing_deg = tilt_bearing_deg;
  tilt_bearing_difference = 0;
  delta_tilt_bearing_deg = 0;  
  windup_tilt_bearing_deg = tilt_bearing_deg;

  prev_tilt_bearing2_deg = tilt_bearing2_deg;
  tilt_bearing2_difference = 0;
  delta_tilt_bearing2_deg = 0;  
  windup_tilt_bearing2_deg = tilt_bearing2_deg;
  
  EWMA_windup_tilt_bearing_deg = 0;  // This will allow for a smooth transition at launch
  EWMA_windup_tilt_bearing2_deg = 0;  // This will allow for a smooth transition at launch

  delta_error_signal = 0;  
  delta_error_signal2 = 0;  

  loopcount = 0;

  spin_rate_dps = 0;
  spin_rate2_dps = 0;  

  PID_Setpoint_rads = 0;
  PID_Setpoint_degs = 0;

  motor.target = PID_Setpoint_rads;

  PreviousPositionRads = 0;
  CurrentPositionRads = 0;

  // Initialize variables for estimating velocity and altitude
  // based on the accelerometer data
  // Since launch has already been detected
  // make a guess-timate of the starting initial vel and pos
  // before entering the actual loop below  
  vel_mps = 3 * 9.81 * 0.01;
  alt_m = vel_mps * 0.01;

  vel2_mps = 3 * 9.81 * 0.01;
  alt2_m = vel2_mps * 0.01;

  BLDC_loop_duration_us = 333;

  ISM330DHCX_CONVERSION = false;

  loop_timer = micros();
  micros_timer = micros();
  prev_micros_timer = micros();
  Timer1 = micros();
  Timer2 = micros();
  Starttime = micros();
  Runtime = millis();
   
}
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

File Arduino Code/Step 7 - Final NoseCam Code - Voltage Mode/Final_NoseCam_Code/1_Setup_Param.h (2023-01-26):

#ifndef _SETUP_PARAM_H
#define _SETUP_PARAM_H

//---------------------------------------------------------------------------------------//

  // The following values are for Adafruit ISM330DHCX accelerometer 
  // bias correction 
  raw_accel_x_offset = 0.000;
  raw_accel_y_offset = 0.000;
  raw_accel_z_offset = 0.000;
  raw_accel_x_scaling = 1.000000;
  raw_accel_y_scaling = 1.000000;
  raw_accel_z_scaling = 1.000000;

  // Adafruit ISM330DHCX gyro correct factor for the rocket vertical (spin) axis
  Z_Gyro_Cal = 1.0000;

  // The following values are for Adafruit ICM20649 accelerometer 
  // bias correction
  raw_accel2_x_offset = 0.000;
  raw_accel2_y_offset = 0.000;
  raw_accel2_z_offset = 0.000;
  raw_accel2_x_scaling = 1.000000;
  raw_accel2_y_scaling = 1.000000;
  raw_accel2_z_scaling = 1.000000;

  // Adafruit ICM20649 gyro correct factor for the rocket vertical (spin) axis
  Z_Gyro2_Cal = 1.0000;

  // These parameters are used to dynamically modify the position (angle)
  // loop Proportional and Derivative gain terms during flight
  // They can also be changed during operation using the Commander Interface
  P_Base = 20;
  P_Gain = 20;
  D_Base = 0;
  D_Gain = 2.00;
  Spin_Rate_Adj = 0.55;


//---------------------------------------------------------------------------------------//

//---------------------------------------------------------------------------------------//


  // SimpleFOC driver config
  // power supply voltage [V]
  driver.voltage_power_supply = 25;
    
  driver.init();
  // link the motor and the driver
  motor.linkDriver(&driver);

  // enable/disable quadrature mode
  encoder.quadrature = Quadrature::ON;

  // check if you need internal pullups
  encoder.pullup = Pullup::USE_EXTERN;
  
  // initialize encoder hardware
  encoder.init();
  // hardware interrupt enable
  encoder.enableInterrupts(doA, doB);
  // link the motor to the sensor
  motor.linkSensor(&encoder);

  Serial.println("Encoder Ready\n");


  // choose FOC modulation
  // FOC torque control requires sinusoidal currents
  // therefore use either Sinusoidal PWM or Space vector PWM
  // FOCModulationType::SinePWM (default)
  // FOCModulationType::SpaceVectorPWM
  // FOCModulationType::Trapezoid_120
  // FOCModulationType::Trapezoid_150
  motor.foc_modulation = FOCModulationType::SinePWM;

  // set torque mode to be used
  // TorqueControlType::voltage  (default)
  // TorqueControlType::dc_current  // requires current sense
  // TorqueControlType::foc_current  // requires current sense
  motor.torque_controller = TorqueControlType::voltage;

  // set motion control loop to be used
  // MotionControlType::torque - torque control 
  // MotionControlType::velocity - velocity motion control
  // MotionControlType::angle - position/angle motion control
  // MotionControlType::velocity_openloop - velocity open-loop control
  // MotionControlType::angle_openloop - position open-loop control
  motor.controller = MotionControlType::angle;


  // controller configuration 
  // default parameters in defaults.h
  // controller configuration based on the control type 

  // aligning voltage [V]
  // A higher value is better in that it results in less measurement noise
  motor.voltage_sensor_align = 6;
  // incremental encoder index search velocity [rad/s]
  motor.velocity_index_search = 1.0; // default 1 rad/s

  motor.voltage_limit = 25;  // Set with ALU

  // angle loop velocity limit // Set using the ALV command
  // initial speed for moving to the correct angular offset
  motor.velocity_limit = 1.0;


  // Other parameters
  motor.PID_velocity.P = 0.50000;
  motor.PID_velocity.I = 5.0000;
  motor.PID_velocity.D = 0.00000;
  motor.LPF_velocity.Tf = 0.010;   // velocity low pass filtering time constant   // smaller means less filtering
  motor.P_angle.P = 40;   // angle loop PID controller parameters   // not used for torque or velocity control
  motor.P_angle.I = 0;
  motor.P_angle.D = 0;     

  
  // jerk control it is in Volts/s or Amps/s
  // for most of applications no change is needed 
  motor.PID_velocity.output_ramp = 1000.0;

  // acceleration limit
  motor.P_angle.output_ramp = 1000.0;
  
  motor.useMonitoring(Serial);

  command.add('A', onMotor, "motor");
  command.add('D', P_Base_Call, "P_Base_Call");
  command.add('E', P_Gain_Call, "P_Gain_Call");
  command.add('F', D_Base_Call, "D_Base_Call");
  command.add('G', D_Gain_Call, "D_Gain_Call");
  command.add('S', Rate_Adj_Call, "Rate_Adj_Call");  // For real-time calibration of the feed forward
  command.add('Z', Z_Gyro_Call, "Z_Gyro_Call");   // For real-time calibration of the Z gyro
  command.add('Y', Z_Gyro2_Call, "Z_Gyro2_Call");   // For real-time calibration of the second Z gyro


#endif  // _SETUP_PARAM_H


/**************************************************************************************/

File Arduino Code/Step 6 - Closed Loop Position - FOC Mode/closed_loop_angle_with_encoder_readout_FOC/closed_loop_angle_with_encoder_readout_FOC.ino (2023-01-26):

// Closed loop motor control example using FOC current control
// Assumes the power supply to the motor amplifier is at 24 volts
#include <SimpleFOC.h>

// BLDC motor & driver instance
BLDCMotor motor = BLDCMotor(11); // 11 pole pairs
BLDCDriver3PWM driver = BLDCDriver3PWM(10, 5, 6, 8);

Encoder encoder = Encoder(2, 3, 2560);
// interrupt routine intialization
void doA(){encoder.handleA();}
void doB(){encoder.handleB();}

// Inline current sensor instance
// Check if your board has R010 (0.01 ohm resistor) or R006 (0.006 mOhm resistor)
InlineCurrentSense current_sense = InlineCurrentSense(0.01, 50.0, A0, A2);

// commander communication instance
Commander command = Commander(Serial);
void onMotor(char* cmd){ command.motor(&motor, cmd); }


float time_delay_micros;

long loopcount = 0;


void setup() {

  Serial.begin(115200);
  delay(1500);

  // driver config
  // power supply voltage [V]
  driver.voltage_power_supply = 24;
  driver.init();
  // link the motor and the driver
  motor.linkDriver(&driver);

  // enable/disable quadrature mode
  encoder.quadrature = Quadrature::ON;
  // check if you need internal pullups
  encoder.pullup = Pullup::USE_EXTERN;
  
  // initialize encoder hardware
  encoder.init();
  // hardware interrupt enable
  encoder.enableInterrupts(doA, doB);
  // link the motor to the sensor
  motor.linkSensor(&encoder);
  Serial.println("Encoder ready\n");

  // current sense init and linking
  current_sense.init();
  motor.linkCurrentSense(&current_sense);

  motor.foc_modulation = FOCModulationType::SpaceVectorPWM;

  motor.torque_controller = TorqueControlType::foc_current;

  motor.controller = MotionControlType::angle;

  // Aligning voltage [V]
  // A higher value is better in that it results in less measurement noise
  motor.voltage_sensor_align = 6;
  // incremental encoder index search velocity [rad/s]
  motor.velocity_index_search = 1.0; // default 1 rad/s

  // set overall motor limits
  motor.voltage_limit = 24; // Set with ALU when running
  motor.current_limit = 4.0; // Set with ALC when running
  motor.velocity_limit = 20;  // Set with ALV when running // Only applies to angle (position) control !!!!!
  motor.P_angle.limit = 20; // MUST follow changes to motor.velocity_limit with same value

  // DC and FOC current torque control PID parameters
  // Q axis parameters
  // not used for voltage torque control
  motor.PID_current_q.P = 5;
  motor.PID_current_q.I = 300;
  motor.PID_current_q.D = 0;
  motor.PID_current_q.limit = motor.voltage_limit; 
  // Low pass filtering
  motor.LPF_current_q.Tf= 0.003;

  // FOC current torque control PID parameters
  // D axis parameters
  // not used for DC current torque or voltage control
  motor.PID_current_d.P = 5;
  motor.PID_current_d.I = 300;
  motor.PID_current_d.D = 0;
  motor.PID_current_d.limit = motor.voltage_limit; 
  // Low pass filtering
  motor.LPF_current_d.Tf= 0.003;
  
  // velocity loop PID controller parameters
  // not used for torque control    
  motor.PID_velocity.P = 0.200;
  motor.PID_velocity.I = 5.000;
  motor.PID_velocity.D = 0.000;

  // jerk control it is in Volts/s or Amps/s
  // for most of applications no change is needed 
  motor.PID_velocity.output_ramp = 1000.0;

  // velocity low pass filtering time constant
  // smaller means less filtering
  motor.LPF_velocity.Tf = 0.010;

  // angle loop PID controller parameters
  // not used for torque or velocity control  
  motor.P_angle.P = 20;
  motor.P_angle.I = 0; // usually set to 0  - P controller is enough
  motor.P_angle.D = 0; // usually set to 0  - P controller is enough
  // acceleration limit
  motor.P_angle.output_ramp = 1000.0; 

  motor.useMonitoring(Serial);

  // set the inital target value
  motor.target = 0.0;

  // initialize motor
  motor.init();

  // align encoder and start FOC
  Serial.println("\n\nAligning the encoder");

  motor.initFOC();

  Serial.println("\n\nEncoder Aligned\n\n");
  
  // subscribe motor to the commander
  command.add('A', onMotor, "motor");  // All commands must start with "A"

  Serial.println("\n\nMotor ready\n\n");

  time_delay_micros = 333;
  
}


void loop() {

  // iterative setting FOC phase voltage
  motor.loopFOC();
  
  // iterative function setting the outer loop target
  motor.move();

  // user communication
  command.run();

  if (loopcount % 1000 == 0) {
    encoder.update();
    Serial.print(encoder.getAngle(),4);
    Serial.print("\t");
    Serial.println(current_sense.getDCCurrent(),2);  
  }

  delayMicroseconds(time_delay_micros);

  loopcount++;
  
}

  /*

  Typical commands for velocity control include the following:

  char* my_string = "ALV10";   
  command.run(my_string);
  
  ? - list all commands
  #5 - set decimal point number to 5
  
  AMG or AMG0 - get motor "A" target

  AMG5 - get motor current velocity
  
  AMG6 - get motor current angular position
  
  A5.0 - set motor "A" target to 5.0
    
  AVP - get motor "A" velocity loop PID proportional gain
  AVP0.15 - set motor "A" velocity loop PID proportional gain to 0.15
  AVI
  AVD
  AVR - get motor "A" velocity loop voltage or current ramp limit
  AVL - get motor "A" velocity loop voltage or current limit
  AVF - get motor "A" velocity loop filter time constant  

  AAP - get motor "A" angle (position) loop PID proportional gain  

  AQP - get motor "A" Q current loop PID proportional gain      
  
  ADP - get motor "A" D current loop PID proportional gain    


  ALC - get motor "A" current limit
  ALU - get motor "A" voltage limit
  ALV - get motor "A" velocity limit

  AE - get motor "A" enable (1) / disable (0) status

  AR - get motor "A" phase resistance

  ASM - sensor offset

  ASE - sensor electrical offset


  PhaseCurrent_s currents = current_sense.getPhaseCurrents();
  float current_magnitude = current_sense.getDCCurrent();

  Serial.print(currents.a*1000); // milli Amps
  Serial.print("\t");
  Serial.print(currents.b*1000); // milli Amps
  Serial.print("\t");
  Serial.print(currents.c*1000); // milli Amps
  Serial.print("\t");
  Serial.println(current_magnitude*1000); // milli Amps

  Serial.println(motor.Ua);
  Serial.println(motor.Ub);
  Serial.println(motor.Uc);   

  Serial.println(motor.voltage.q);  
  Serial.println(motor.voltage.d); 
   
  Serial.println(motor.current.q);  
  Serial.println(motor.current.d); 

  Serial.println(motor.shaft_velocity);   
  Serial.println(motor.shaft_velocity_sp);  


  */
  
  /*
  
    // Some useful commands - substitute "encoder" for "sensor" as needed 
    sensor.getMechanicalAngle();
    sensor.getAngle();    
    sensor.getPreciseAngle();
    sensor.getVelocity();
    sensor.getFullRotations(); 
    sensor.update(); 
  
    sensor offset [rad]
    motor.sensor_offset = 0; // default 0 rad
  
    motor.enable(); // just a test
    motor.disable(); // just a test
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

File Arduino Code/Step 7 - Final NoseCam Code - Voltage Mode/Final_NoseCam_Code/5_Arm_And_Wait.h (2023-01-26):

#ifndef _ARMANDWAIT_H
#define _ARMANDWAIT_H


  motor.velocity_limit = 10;
  motor.P_angle.limit = 10; // MUST follow changes to motor.velocity_limit

  motor.PID_velocity.P = 0.20000;
  motor.PID_velocity.I = 2.00000;
  motor.PID_velocity.D = 0.00000;
  motor.LPF_velocity.Tf = 0.010;   // velocity low pass filtering time constant   // smaller means less filtering
  motor.P_angle.P = 10;   // angle loop PID controller parameters   // not used for torque or velocity control
  motor.P_angle.I = 0;
  motor.P_angle.D = 0;  


  loopcount = 1;
  
  while (!ARM) {

    motor.loopFOC();
    motor.move();

    if ( loopcount % 3000 == 0 ) {
  
      loopcount = 0;     
      
      Serial1.println("Type ARM to continue ...........\n");  
  
      while (!ARM && Serial1.available() > 0) {   
        // get the new byte:
        char inChar = Serial1.read();
        // add it to the inputString:
        Incoming += inChar;    
        if (inChar == '\n') {
          Serial1.println(Incoming);
          if (Incoming.indexOf("ARM") >= 0) {
            Serial1.println("System Armed\n\n");
            ARM = true;
          }
  
          else Serial1.println("No Match\n");
          
          Incoming = "";        
          
        }
  
      }  
    
    }
  
    delayMicroseconds(500);
    
    loopcount++;

  }

  while (Serial1.available() > 0) Serial1.read(); // clear buffer 

  
  /*-------------------------------------------------------------------------------------------------*/
  /*-------------------------------------------------------------------------------------------------*/  


  Serial1.println("Powering camera\n\n\n");  
  digitalWrite(POWER_SWITCH, HIGH);  // Pin 12 controls power to the camera
  delay(1000);


  // Initialize the accelerometer and gyro EWMA filters

  /* Get new sensor events */ 
  ism330dhcx.getEvent(&accel, &gyro, &temp);  // About 200us for a single SPI bus conversion

  raw_accel_x_corrected = (accel.acceleration.x - raw_accel_x_offset) * raw_accel_x_scaling;
  raw_accel_y_corrected = (accel.acceleration.y - raw_accel_y_offset) * raw_accel_y_scaling;
  raw_accel_z_corrected = (accel.acceleration.z - raw_accel_z_offset) * raw_accel_z_scaling;

  accel_x_ewma = raw_accel_x_corrected;
  accel_y_ewma = raw_accel_y_corrected;
  accel_z_ewma = raw_accel_z_corrected;
  accel_x_old_ewma = accel_x_ewma;
  accel_y_old_ewma = accel_y_ewma;
  accel_z_old_ewma = accel_z_ewma;

  gyro_x_ewma = gyro.gyro.x;
  gyro_y_ewma = gyro.gyro.y;
  gyro_z_ewma = gyro.gyro.z;
  gyro_x_old_ewma = gyro_x_ewma;
  gyro_y_old_ewma = gyro_y_ewma;
  gyro_z_old_ewma = gyro_z_ewma;


  icm20649.getEvent(&accel, &gyro, &temp);  // About 300us for a single SPI bus conversion


  // Perform offsets and corrections
  raw_accel2_x_corrected = (accel.acceleration.x - raw_accel2_x_offset) * raw_accel2_x_scaling;
  raw_accel2_y_corrected = (accel.acceleration.y - raw_accel2_y_offset) * raw_accel2_y_scaling;
  raw_accel2_z_corrected = (accel.acceleration.z - raw_accel2_z_offset) * raw_accel2_z_scaling;

  accel2_x_ewma = raw_accel2_x_corrected;
  accel2_y_ewma = raw_accel2_y_corrected;
  accel2_z_ewma = raw_accel2_z_corrected;
  accel2_x_old_ewma = accel2_x_ewma;
  accel2_y_old_ewma = accel2_y_ewma;
  accel2_z_old_ewma = accel2_z_ewma;

  gyro2_x_ewma = gyro.gyro.x;
  gyro2_y_ewma = gyro.gyro.y;
  gyro2_z_ewma = gyro.gyro.z;
  gyro2_x_old_ewma = gyro2_x_ewma;
  gyro2_y_old_ewma = gyro2_y_ewma;
  gyro2_z_old_ewma = gyro2_z_ewma;


  Incoming = "";  
  loopcount = 0;
  loop_timer = micros();


  motor.PID_velocity.P = 0.10000;
  motor.PID_velocity.I = 1.0000;
  motor.PID_velocity.D = 0.00000;
  motor.LPF_velocity.Tf = 0.020;   // velocity low pass filtering time constant   // smaller means less filtering
  motor.P_angle.P = 5;   // angle loop PID controller parameters   // not used for torque or velocity control
  motor.P_angle.I = 0;
  motor.P_angle.D = 0;

  /*-------------------------------------------------------------------------------------------------*/
  /*-------------------------------------------------------------------------------------------------*/  


  while (!LAUNCH) {

    while ((micros() - loop_timer) < target_loop_rate_us) {
      motor.loopFOC();
      motor.move();
      delayMicroseconds(500);
    }

    loop_timer = micros();

    loopcount++;
  
    while (!LAUNCH && Serial1.available() > 0) {   
      // get the new byte:
      char inChar = Serial1.read();
      // add it to the inputString:
      Incoming += inChar;    
      if (inChar == '\n') {
        Serial1.println(Incoming);
        if (Incoming.indexOf("LAUNCH") >= 0) {
          Serial1.println("Launch !!!!!\n");
          LAUNCH = true;
        }

        else Serial1.println("No Match\n");
        
        Incoming = "";        
      }

    }


    // Get new sensor events 
    ism330dhcx.getEvent(&accel, &gyro, &temp);  // About 200us for a single SPI bus conversion

    PrevConversionTimer = ConversionTimer;
    ConversionTimer = micros();
    ConversionTimeMicros = ConversionTimer - PrevConversionTimer;
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
